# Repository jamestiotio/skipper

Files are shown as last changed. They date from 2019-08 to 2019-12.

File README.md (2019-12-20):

# Skipper

**_SUTD 2019 10.002 Physics I 1D Project (19F07 Group 8)_**

## Inspiration

We were inspired by [Skippa](https://youtu.be/M0_U1FHwACk "Skippa by Mark Rober"), a rock-skipping device built by Mark Rober.

## Design Choices

1. With a budget limit of SGD$60, the clay pigeon thrower used by Mark Rober was out. Thus, we (tried to) build the whole device from scratch. This implies that we utilised a simpler throwing mechanism.
2. Materials used:

  * Plywood and acrylic for the thrower
  * PVC pipes and mahogany wood for the base
  * Polymer clay for the stones

## Final Prototype

<p align="center">
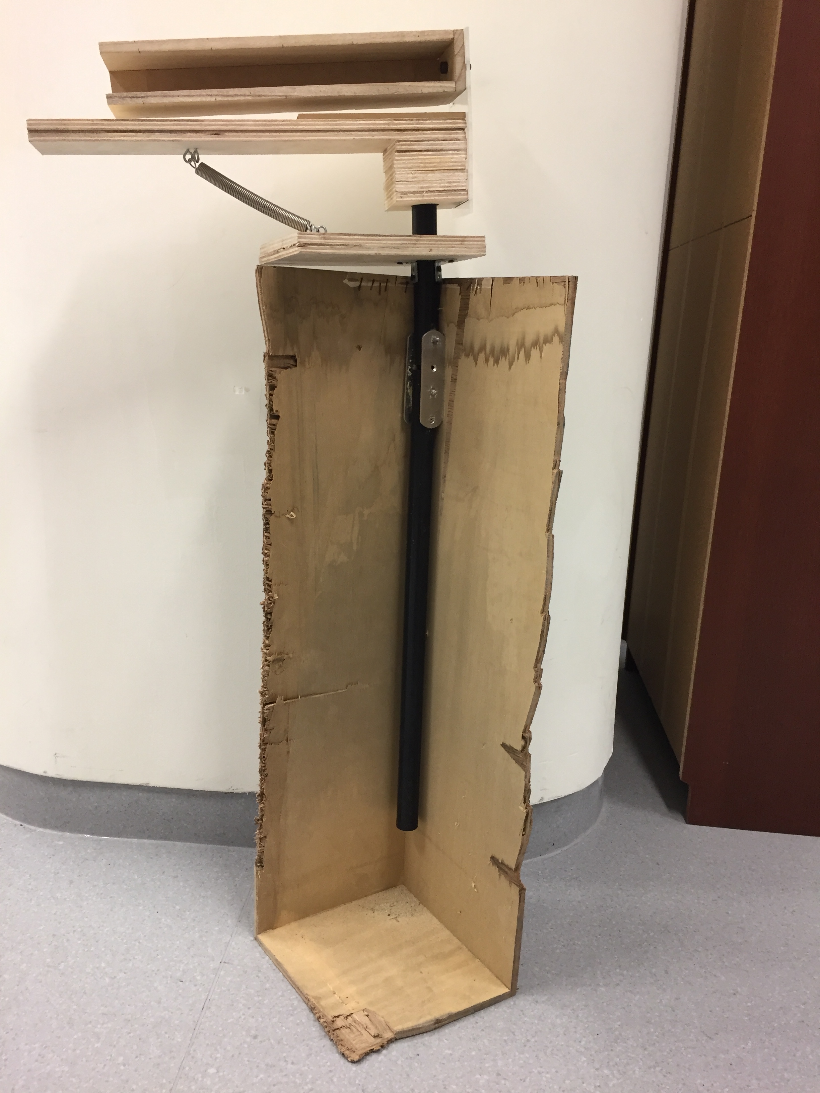
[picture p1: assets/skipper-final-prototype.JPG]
    
</p>

Our best attempt in terms of number of skips (yep, that's me in the yellow-green T-shirt):

best-attempt

[Bill of materials](./Skipper-BOM.xlsx), [CAD file v1.0](./Skipper-Assembly.step) and [our project report](./Physics_1D_F07-Grp08.pdf) are included in this repository.

Do take note that the spring is not included in the CAD file. The 'Base' part in the CAD file is not essential since it serves only as an anchoring foundation at the beach. Keep in mind that the CAD file is a work-in-progress.

## Acknowledgement

This project was made possible by my professors ([Ching Chee Leong](https://academics.sutd.edu.sg/faculty/ching-chee-leong/ "Ching Chee Leong") and [Kwan Wei Lek](https://epd.sutd.edu.sg/people/faculty/kwan-wei-lek "Kwan Wei Lek")) and my teammates, who supported my crazy initial idea of building this prototype and believed in the project until its completion.

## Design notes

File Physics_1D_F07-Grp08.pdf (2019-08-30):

Skipper

James Raphael Tiovalen, Charis Chong En Xin, Hou Bowen, Li Jiaqi, Wong Wei Heng Singapore University of Technology and Design 8 Somapah Rd, Singapore 487372

I. INTRODUCTION

Nearly everyone has tried to throw a stone on a body of water and count the number of skips the stone was able to make. Of course the more, the better. Intuitively, there are some empirical rules for the best throw – one should throw circular and flat stones with a high speed, a small angle with the water surface and with a flick of the wrist to give the stone a spin. These rules can also be understood using the laws of physics. The collision between the stone and the water surface is quite complex because it involves the fluid dynamics around the immersed stone.¹,2 Energy dissipation and angular destabilisation contribute to the sinking of the stone after a few rebounds.

This paper will consider a very simplified description of the motion of a stone skipping over a water surface using forces, momentum and energy. This paper will also propose the creation of a device which could help us determine the best conditions for a significant amount of skips.

II. MOTIVATION AND CREATIVITIES

We were inspired by Skippa, a rock-skipping device built by Mark Rober.³ Several customisations that we imple-mented include:

1. We used cheaper alternatives as our budget limit was $60. This implied that we could not purchase the clay pigeon thrower used by Mark Rober, especially since the clay pigeon thrower exceeds $100 and that it could only be obtained from the United States of America with a long shipping duration. Thus, we built the whole device from scratch.
2. We used wood for the thrower, PVC pipes for the base and polymer clay as the material for the modelled circular stones.
III. | RESULT AND ANALYSIS
Stone No. | Diameter / mm | Thickness / mm | Hand Angle / ◦ | Spring Extension / mm | No. of Skips
1 | 40.5 | 10.5 | 0 | 150 | 1
2 | 40.5 | 10.5 | 5 | 150 | 5
3 | 40.5 | 10.5 | 10 | 150 | 3
4 | 40.5 | 10.5 | 15 | 150 | 1
5 | 40.5 | 10.5 | 0 | 210 | 2
6 | 40.5 | 10.5 | 5 | 210 | 7
7 | 40.5 | 10.5 | 10 | 210 | 2
8 | 40.5 | 10.5 | 15 | 210 | 1
9 | 45.0 | 15.0 | 0 | 150 | 0
10 | 45.0 | 15.0 | 5 | 150 | 4
11 | 45.0 | 15.0 | 10 | 150 | 2
12 | 45.0 | 15.0 | 15 | 150 | 1
13 | 45.0 | 15.0 | 0 | 210 | 3
14 | 45.0 | 15.0 | 5 | 210 | 4
15 | 45.0 | 15.0 | 10 | 210 | 2
16 | 45.0 | 15.0 | 15 | 210 | 1
P. S. We were also able to skip the stones on the sand.

We used a constant distance of the stone from the pivot of 155 mm and a constant arm angle of 0◦ .

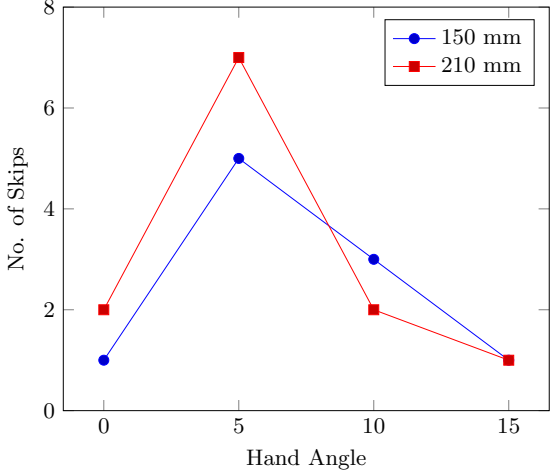
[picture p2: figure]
Hand Angle; No. of Skips

(a) Stone with 40.5 mm diameter and 10.5 mm thickness.

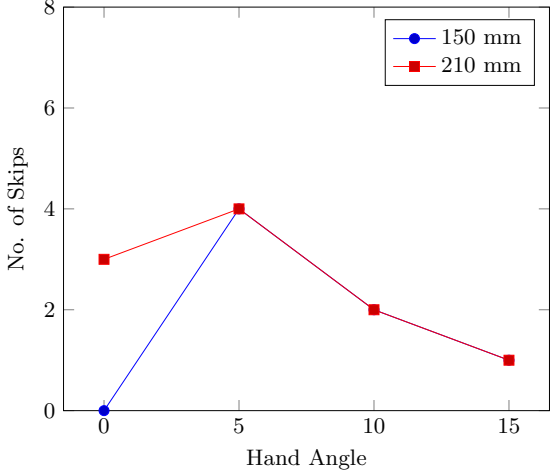
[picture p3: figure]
Hand Angle; No. of Skips

(b) Stone with 45.0 mm diameter and 15.0 mm thickness.

FIG. 1: Plots for the two different stones.

A. Force Analysis

vx0

fs

φ˙
0
(a) Stone at the launcher part of the device (top-view).

−kˆ

v

θ

L

fk
Mg
(b) Stone when it touches the water surface (side-view).

FIG. 2: Free body diagrams for the stone at different times.

The long runway of the thrower’s ‘hand’ allows static friction in the direction parallel to the thrower’s long axis to act on the stone for a longer time (as shown in Figure 2a) and thus the stone would achieve more angular momentum at the end, achieving more angular stability. Meanwhile, the component of static friction in the direction perpendicular to the thrower’s long axis pushes the stone forward, increasing its vx0.

When the stone collides with the water surface, the equations of motion for the stone’s center of mass are

M

dvx
dt = −

1
2

ρwv

2Aim (Cl sin θ + Cf cos θ) | (1a)

M

dvz
dt = −Mg +

1
2

ρwv

2Aim (Cl cos θ − Cf sin θ), | (1b)

where M is the mass of the stone, v is the velocity of the stone (with v

2 = v

2
x + v

2
z

), g is acceleration due to gravity, Aim is the immersed area of the stone in contact with the water surface, Cl and Cf are the lift and friction coefficients respectively, ρw is the mass density of water and θ is the tilt angle of the stone with the water surface. In our case, θ is the same as the hand angle as our arm angle is constantly 0◦
. Note that we do not take into consideration the value of vy as it approximately does not contribute to the number of skips achieved by the stone. The value of vy will only determine how much the stone’s path will bend from its initial straight path when it was launched from the device.

For a circular stone, the immersed area Aim is given by

Aim(s) = R

2

"
cos⁻¹
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
, | (2)

where s =

|z|
sin θ

(the maximum immersed height) and R is the stone’s radius.

The condition for the stone to skip is that a maximum depth must be reached before the stone is fully immersed. By using the constant energy condition of the system and some dimensionless variables (derived by Lyd´eric Bocquet),⁴ we could explicitly solve the condition for skimming to be

vx0 > vc =

s
4Mg sin θ
πR²Cρw sin θ − M tan² β
, | (3)

where vc is the minimum critical velocity, tan β =

vz0
vx0

and C = Cl cos θ − Cf sin θ ≈ Cl .

More skips could be achieved if vc is lower. This would mean a smaller vz0, a larger vx0, a smaller M and a larger
R. This confirms our intuition of throwing a light and flat stone with a high linear speed with an initial height as close to the water surface as possible. In our case, since we are using polymer clay with a uniform density to craft the stones, an increase in R would inevitably lead to an increase in M. Thus, based on our data, the bigger stone achieves a lower number of skips due to this effect. Furthermore, both the numerator and the denominator contain sin θ, which makes the determination of the relationship of the number of skips with θ difficult. We will attempt to find this relationship using other methods.
B. Momentum Analysis

+y

−x

−z

ω

FIG. 3: Graph of the stone’s rotation in 3D. Stone is depicted as a 2D circle for simplification purposes.

By using Euler equations, we could derive the equation for the tilt angle, θ, of the stone with respect to the surface of water to be

¨θ +

φ˙
0
J0 − J1
J1

2
(θ − θ0) = Mθ
J1
, | (4)

where φ˙
0 is the initial spin angular velocity, θ0 is the initial tilt angle of the stone before its first skip, J0 and J1 are moments of inertia of the stone in the directions normal and along the stone respectively and Mθ is the projection of the torque due to water flow in the y-direction. Thus, for a successful skip, θ needs to remain approximately constant. The condition for this is described as

φ˙
0 ≈ ω

r
g
R
. | (5)

This is supported by our data, which shows how the stone with a larger radius would achieve a lower initial angular velocity, and thus would skip less due to it possessing less angular stability.

From Lyd´eric Bocquet´s research paper,⁴
the number of skips achieved by the stone, Nc, can be non-prescriptively approximated by the equation

Nc ≈

Rφ˙
0

2

g

. | (6)

This is obtained by considering angular destabilisation of the stone. This is supported by our experimental data, which shows that as the spring extension is increased, the maximum angular speed achieved would be larger and thus φ˙
0 would be higher. Unsurprisingly, the stone with a smaller radius achieved more number of skips. This could be due to the fact that it requires more time for the larger stone to reach the same φ˙
0. As φ˙
0 contributes quadratically, compared to the linear contribution of R, φ˙
0 has a more significant impact on the value of Nc. Thus, considered together, this would correspond to a higher Nc.
C. Energy Analysis

By only considering the x-component of the stone’s velocity and neglecting wind and air friction, after each collision with the water surface, the loss in kinetic energy of the stone is approximately given by

W = −

Z t

0

Fx(t)vx(t) dt ≈ −µMg`, | (7)

where t is the collision time, µ =

Cl sin θ+Cf cos θ
C

and ` is defined as

` = vx0

2π
ω0

= 2π

s
M sin θ
CρwR
. | (8)

Thus, after N collisions, the velocity of the stone obeys the relation

1
2

Mvxf

2 −

1
2

Mvx0

2 = −NµMg`, | (9)

where the number of skips Nc will be when the total energy loss is larger than the initial kinetic energy. Hence, Nc is given accordingly by

Nc =

vx0

2
2gµ` . | (10)

This is supported by our data, which indicates that a higher vx0 due to a larger spring extension would lead to a larger Nc. The relationship of Nc with θ is still yet unclear since both ` and µ are dependent on the value of θ. Considering ` only, we would like the value of θ to be as small as possible to achieve a larger Nc. However, our data
shows that a value of θ = 5◦ would lead to a higher number of skips than θ = 0◦ | . This might be due to some alteration
to the final value of Nc by µ. Thus, our ‘sweet spot’ is the value of θ = 5◦

IV. CHALLENGES AND SOLUTIONS

1. The pivot between the thrower and the base column was too weak since it was made from acrylic. This causes the thrower to oscillate too much as it is not so stable. This could lead to the further end of the thrower stealing some energy from the stone and disrupts the rotation of the stone if the stone collides with the thrower. An improvement would be to cut metal with waterjet to replace the whole pivot connection. This would strengthen the connection and prevents unnecessary oscillations.

2. The spring that we obtained is not strong enough and thus the stones were only able to skip a maximum of 7 times. A possible improvement would be to utilise a stronger spring with a larger spring constant.
3. The polymer clay is of a low density and the stones actually float in seawater. This causes the reaction buoyant force to be lower than expected and thus the stone would skip lower than expected.
4. We conducted our data collection at Siloso Beach, Sentosa Island, Singapore. At the beach, the surface of water oscillates with the ocean waves and tides. This alters the shape of the water surface and thus, the direction of forces would be different compared to a flat body of water. At the beach, due to the temperature and pressure gradient between the land area and the sea area, winds are frequent. This also hinders us from achieving accurate readings as the winds would exert additional forces on the stone that was being skipped. An improvement that could be done would be to conduct the testing at a water reservoir or a swimming pool with no or less winds and a flat surface of water.
5. The PVC pipes were not very strong. As such, the PVC pipes actually bend towards its insides as we tried to tighten the bolt. Thus, a possible improvement would be to use metal for the whole pivot column connected to the base.
6. The plane of the beach’s surface had a non-zero angle with respect to the surface of the water. This would lead to a systematic error of the angle measured.
7. Our mechanism assumes that the spring solely extends linearly with no bending. In reality, with the structure that we have built, the spring would bend a little as it is bent through the angle when the thrower is turned.
8. It is assumed that:
(a) The mass of the polymer clay stays constant throughout its motion.
(b) The shape of the polymer clay stays constant throughout its motion, i.e. the stones are rigid.
(c) The angle of attack, α, remains constant along each impact with the water.

If any of these assumptions are not true, the theoretical calculations that we performed would be less accurate.

V. CONCLUSION AND FUTURE WORK

We succeeded in determining the important factors that affect the maximum number of skips of the stone. Based on our experiments, an arm angle of 5◦ with a fairly strong initial force is optimal to achieve the most number of skips. This differs with the empirical result of a research paper⁵

that discovered 20◦ as the ‘magic’ angle. Also, we were only able to achieve single-digit numbers of skips. This might be due to the accumulation of all the different inaccuracies. For further improvement, we could construct a properly structured base with a low centre of gravity to further stabilise the device, instead of just weighing down the base with sand of half the base’s height. With a stronger base, we would not require to fix the hand and thus the hand angle would also be able to be changed. We could also follow Mark Rober’s mechanism instead of our current mechanism to prevent the bending of the spring. Finally, a high-speed camera mounted on a drone could be used in order for us to be able to experimentally determine the value of the stone’s angular velocity at any point in time during the stone’s collisional process.

REFERENCES

1 C. L. Stong, The Amateur Scientist, Scientific American 219 (2), 112–118 (1968).
2 H. R. Crane, “How things work: What can a dimple do for skipping stones?”, The Physics Teacher 26 (5), 300–301 (1988). 3 M. Rober, “Rock Skip Robot - The SCIENCE of PERFECT ROCK SKIPPING”, YouTube (2018).
4 L. Bocquet, “The physics of stone skipping”, arXiv (2002).
5 L. Rosellini, F. Hersen, C. Clanet and L. Bocquet, “Skipping stones”, Cambridge University Press (2005).

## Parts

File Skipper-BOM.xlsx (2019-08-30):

Item | Amount w/o GST (S$) | GST (S$) | Total Amount with GST (S$)
Stock Extension Spring SSE-160180-4S | 6.32 | 0.44 | 6.76
MDF 11.81x7.87x0.24inch | 1.87 | 0.13 | 2.00
Board 400x12x90mm | 3.74 | 0.26 | 4.00
Plywood 500x500x12mm | 15.00 | 1.05 | 16.05
32mm uPVC Pipes | 3.55 | 0.25 | 3.80
M4x45mm Screws | 14.00 | 0.00 | 14.00
M4x30mm Screws | 12.50 | 0.00 | 12.50
Heavy Mahogany Box Base | (We obtained this box free-of-charge.)
 | Grand Total Amount |  | 59.11

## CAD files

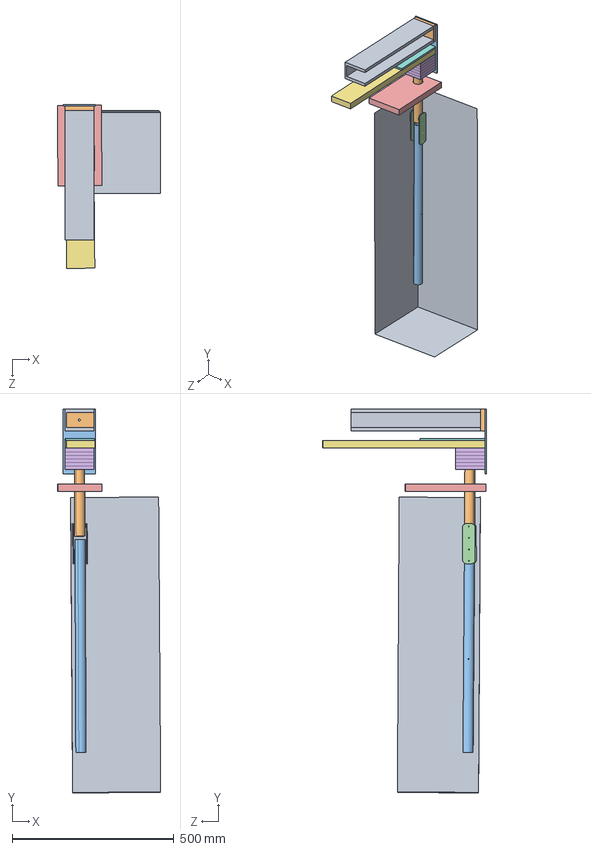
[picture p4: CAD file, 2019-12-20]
Skipper-Assembly.step
319.2 x 1185.4 x 505.8 mm
Upper_Arm
Lower_Arm
Metal_Connector x 2
Base
Hand_Base
Hand_Neck x 6
Long_Hand_Upper_Base
Long_Hand_Upper_Connector
Main_Thrower
Thrower_Connector
Acrylic_Connector

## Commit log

2019-08-30 Upload project files
    [Skipper-BOM.xlsx]
2019-12-20 Add overall CAD file
    [Skipper-Assembly.step]
